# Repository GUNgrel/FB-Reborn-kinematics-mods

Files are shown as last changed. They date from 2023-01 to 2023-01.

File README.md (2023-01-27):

<br/>
<p align="center">
  <a href="https://github.com/GUNgrel/FB-Reborn-kinematics-mods">
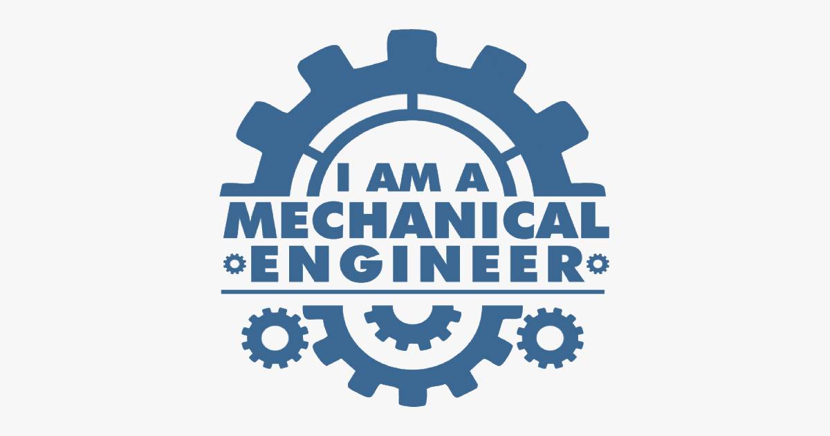
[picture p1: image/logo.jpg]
    
  </a>

  <h3 align="center">Flying Bear Reborn Kinematics mods</h3>

  <p align="center">
    <a href="https://github.com/GUNgrel/FB-Reborn-kinematics-mods"><strong>ВСЕ ФАЙЛЫ ПРОЕКТА</strong></a>
    <br/>
    <br/>
  </p>
</p>

## О проекте

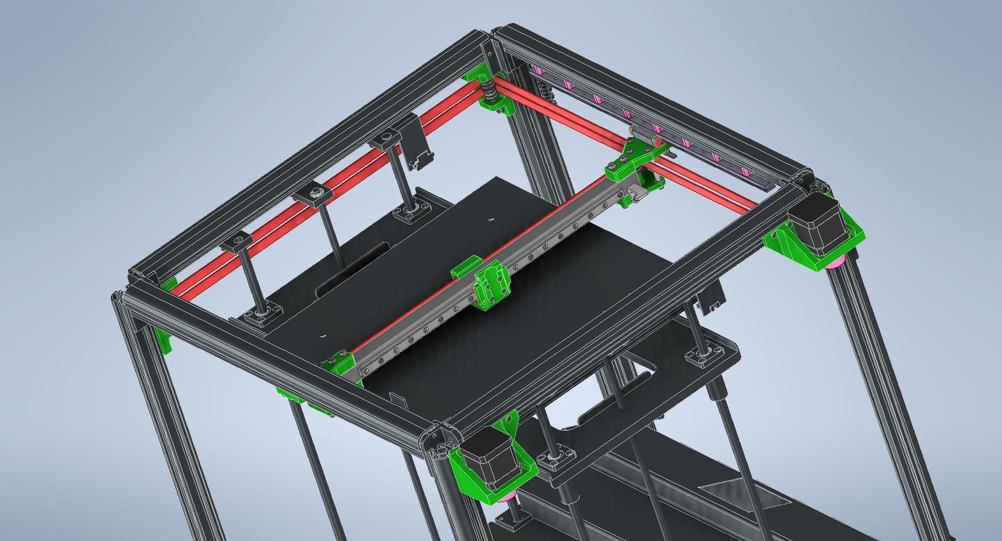
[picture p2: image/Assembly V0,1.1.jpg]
  

  Я очень давно хотел перейти на своём 3д принтере Flying Bear Reborn на рельсы MGN12 и ремни 10 мм, но все существующие проекты так или иначе меня не устраивали.
Поэтому я решил создать собственный проект комплексной замены кинематики по осям Х и У.
  Так сказать "с преферансом и куртизанками" 
  
  Данный проект предусматривает установку головы от [Ruslan P](https://t.me/pavluchenkor) - [Бшня Микшки](https://github.com/pavluchenkor/BearTower)

## Программное обеспечение

I design in Autodesk Inventor 2022

### Что вам понадобится для сборки этого мода:

 ИНСТРУМЕНТЫ
1. Немного прямых рук)
2. Минимальный набор шестигранников.
3. Мини УШМ или ножовка по металлу.
4. Дрель и сверло 3(3.2) и 6 мм.
  
 ПОКУПКИ

   1. [ВЕДОМОСТЬ ПОКУПНЫХ ИЗДЕЛИЙ](https://github.com/GUNgrel/FB-Reborn-kinematics-mods/raw/main/XLS/Purchase_list.xlsx) 

   2. [ВЕДОМОСТЬ КРЕПЁЖНЫХ ИЗДЕЛИЙ](https://github.com/GUNgrel/FB-Reborn-kinematics-mods/raw/main/XLS/Screws_and_nuts.xlsx)

### СБОРКА

Сборка надо начинать с печати всех или нужны вам деталей.

Если у вас уже установлены рельсы снизу профилей, то проставки для рельс MGN12 печатать не надо.

### <b>Балка У</b>

Для определения сторон – принтер ориентирован при просмотре моторами к зрителю.

Для сборки балки У

Вместо карбоновой трубы возможно использовать профиль 2020.
Длинна трубы или профиля 400 мм. За счёт  пропилов возможна небольшая регулировка по длинне балки в сборе. Принтеры немного отличаются друг от друга.

1.	Если вы используете карбоновую квадрат трубу, то в ней необходимо пропилить с торцов паз шириной 6 мм и длиной 25мм. 

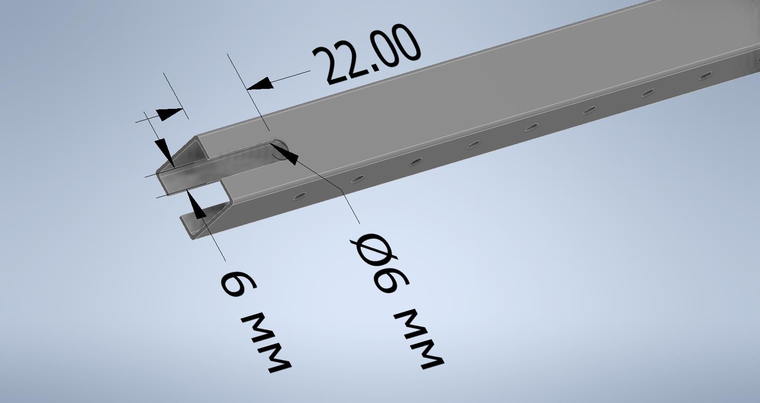
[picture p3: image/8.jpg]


Просверлите отверстия крепления рельсы к балке, используя рельсу для разметки (можно крепить через одно отверстие). 

Для крепления рельсы распечатайте полосу под гайки М3 - nut strip for MGN9 rail. 

Если используете рельсу MGN12 то полоса под гайки - nut strip for MGN12 rail.

Вместо карбоновой трубы возможно использовать профиль 2020.

2.	Далее собираете кронштейны балки. Правый кронштейн имеет отверстия для крепления флажков концевиков Х и У. 

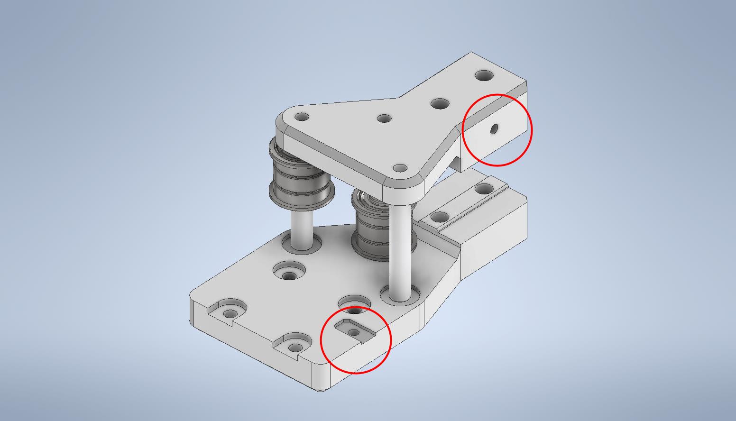
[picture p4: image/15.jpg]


Левый кронштейн без отверстий под флажки концевиков 

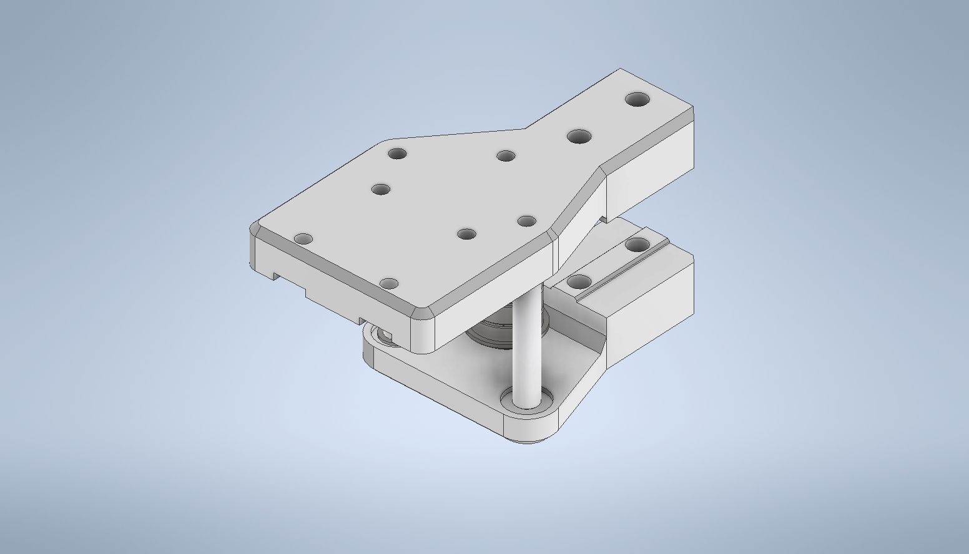
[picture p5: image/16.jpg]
 

Для сборки кронштейнов понадобятся детали:

Штифт 5х30 (резьба М3 с двух сторон) – 6шт

Подшипники F695ZZ -  8 шт

Подшипник 695ZZ – 4 шт.

Винт М3х12 – 12 шт.

Винт М4х50 – 4 шт.

Шайбы М3- 24 шт.

Шайбы М4- 8 шт.

Гайки М4 самоконтрящиеся – 4 шт.

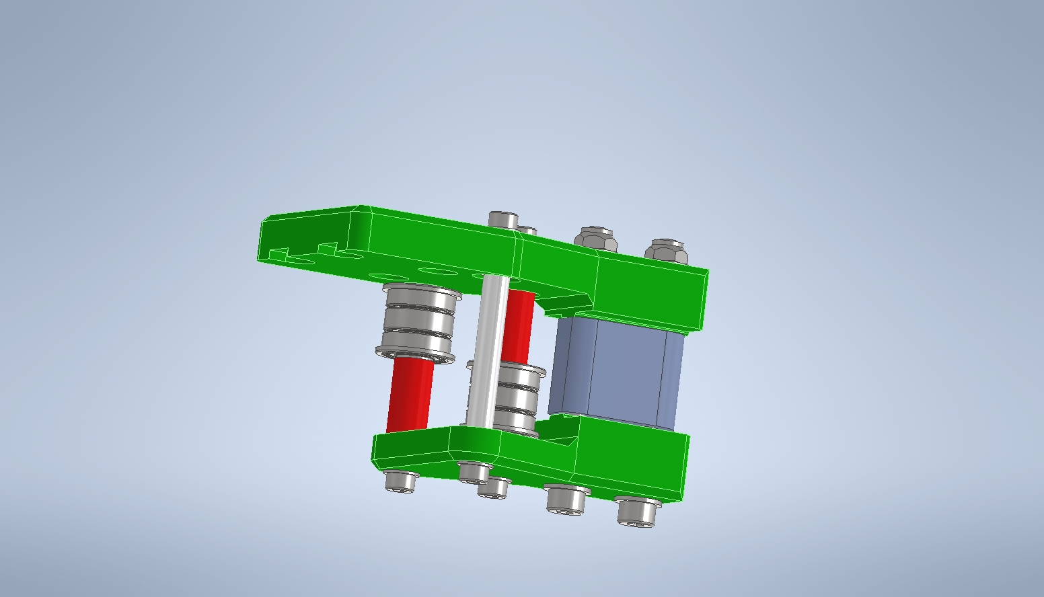
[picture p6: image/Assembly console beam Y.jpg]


Подробнее смотри файл сборки -  [Assembly console beam Y](https://github.com/GUNgrel/FB-Reborn-kinematics-mods/raw/main/STEPs/Assembly_console_beam_Y.stp)

3.	Сборка балки Y

Вставьте балку с рельсой в кронштейны. Винты М4 затягивать после установки на рельсы MGN12 и выставления перпендикулярности. 

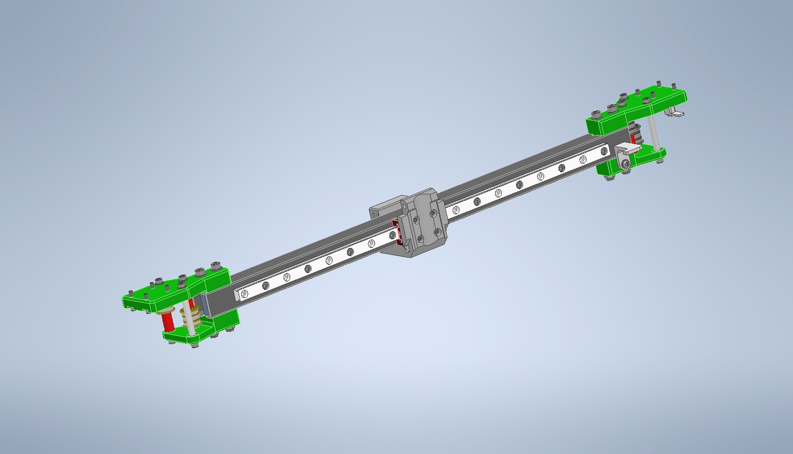
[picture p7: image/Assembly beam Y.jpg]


Подробнее смотри файл сборки - [Assembly beam Y](https://github.com/GUNgrel/FB-Reborn-kinematics-mods/raw/main/STEPs/Assembly_beam_Y.stp)

### Сборка рельс оси Х

Печатаем проставки – 16 шт (из расчёта на рельсу длинной 400мм). Вставляем закладные гайки М3. 

Крепим по 8 шт. с каждой стороны рамы винтами М4х10 и Т-гайками М4.  

НЕ ОБТЯГИВАТЬ.

Крепим рельсу c кареткой на проставки винтами М3х12 

НЕ ОБТЯГИВАТЬ.

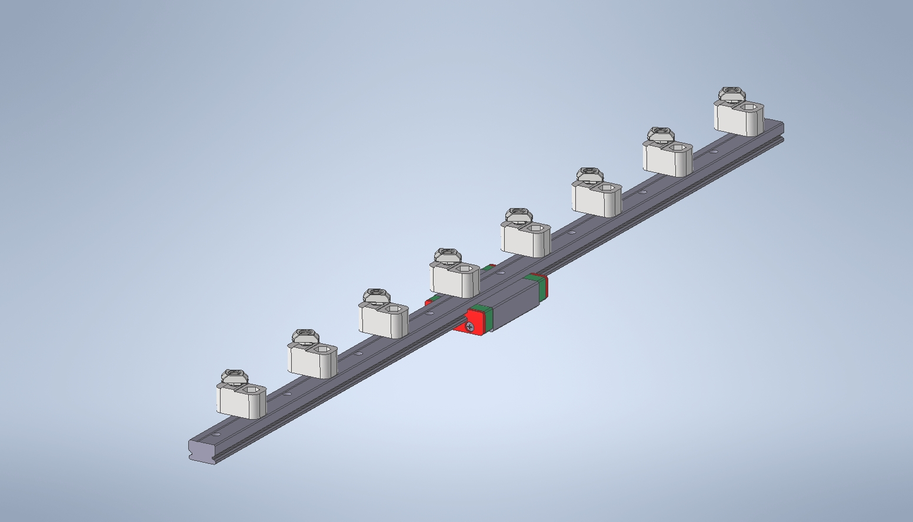
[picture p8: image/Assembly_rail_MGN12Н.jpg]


Подробнее смотри файл сборки - [Assembly_rail_MGN12Н](https://github.com/GUNgrel/FB-Reborn-kinematics-mods/raw/main/STEPs/Assembly_rail_MGN12Н.stp)

### Настройка параллельности и перпендикулярности осей Х и У

Готовьтесь много крутить крепёж…

Сначала выставьте рельсы приблизительно параллельно друг другу, я использовал кусок вала 8 мм. Главное одинаковое расстояние. 

Затем смонтируйте собранную балку У на рельсы Х. Кронштейн балки У сильно не обтягивать. Не затянутый крепёж карбоновой трубы позволит немного смещать её вдоль оси Y, что даст точно выставить расстояние между кронштейнами балки Y.

Теперь с помощью угольника выставите 90 градусов между рельсой Х и рельсой У.

Затяните крепёж кронштейна балки Y с той стороны, где установлен угольник.

Двигайте вперёд и назад балку Y. Она выставит на нужное расстояние вторую рельсу. 

Затяните весь крепёж. Без фанатизма) Детали пластиковые. Лучше добавьте синий фиксатор резьбы.

### МОТОРЫ

Есть два варианта расположения моторов 

## Снаружи 

В этом случае кронштейны разные. Печатать отдельно

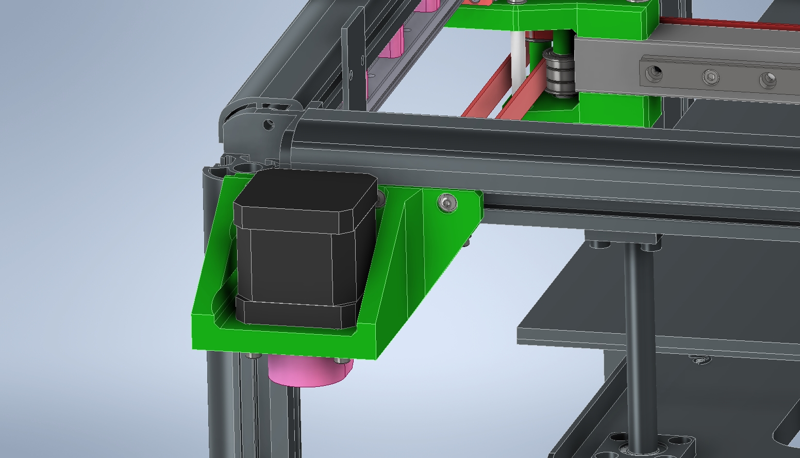
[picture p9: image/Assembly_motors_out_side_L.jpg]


[Console_left_motor](https://github.com/GUNgrel/FB-Reborn-kinematics-mods/blob/main/STEPs/Console_left_motor.stp)

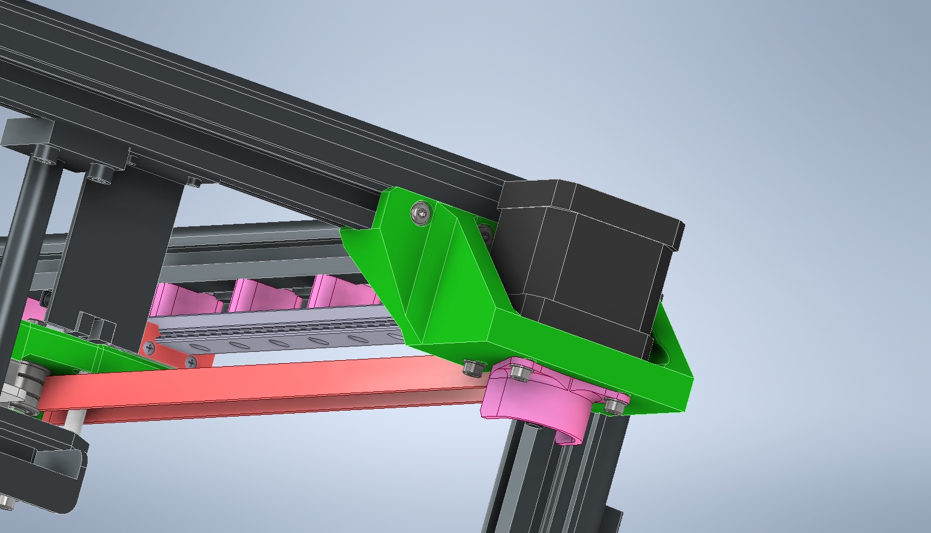
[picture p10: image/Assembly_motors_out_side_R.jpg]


[Console_right_motor](https://github.com/GUNgrel/FB-Reborn-kinematics-mods/blob/main/STEPs/Console_right_motor.stp)

## Внутри 

В этом слусае кронштейны одинаковые с права и лева. Один монтируется ниже другого. Печаталь зеркально на поддержках. 

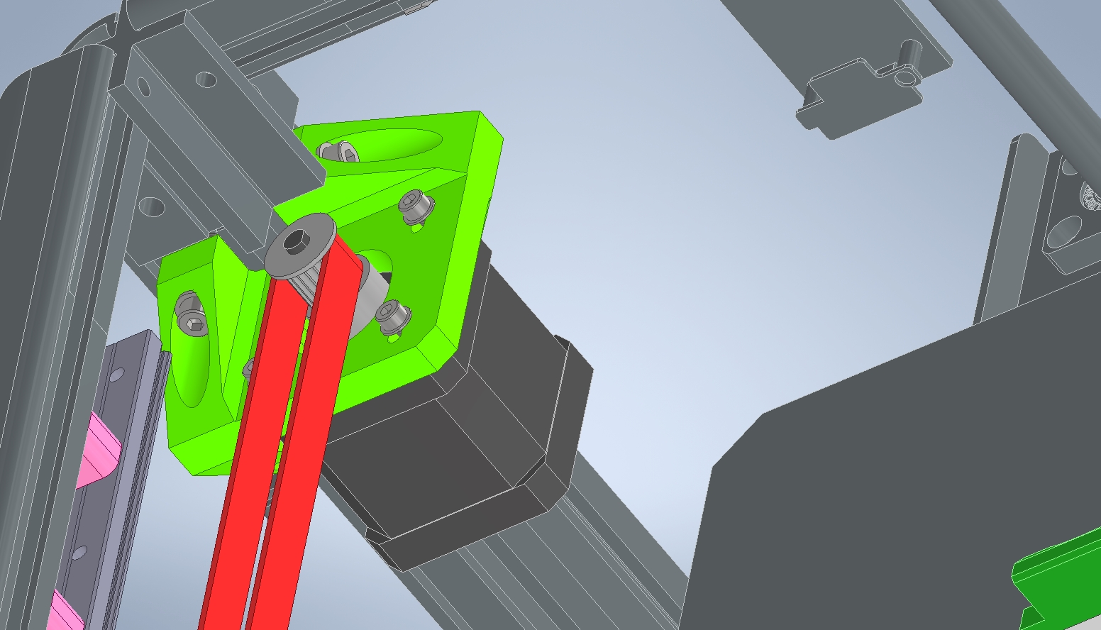
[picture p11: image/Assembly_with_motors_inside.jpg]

 
[Console_moto_inside](https://github.com/GUNgrel/FB-Reborn-kinematics-mods/blob/main/STEPs/Console_moto_inside.stp)

## Автор

* **Alexey Khripyakov** - *Engineer constructor* - [Telegram](https://t.me/gungrel)

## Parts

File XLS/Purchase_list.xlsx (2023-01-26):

Шайбы 5х7 разной толщны | https://aliexpress.ru/item/1005003719920719.html?sku_id=12000026928248768
Шайбы 3х7х0.5 | https://aliexpress.ru/item/1005003719920719.html?sku_id=12000026928248768
Втулка дистанционная М5х9х14 | https://aliexpress.ru/item/32542380485.html?sku_id=12000028149918777 | Можно напечатать
Штифт 5х30 (резьба М3 с двух сторон) | https://aliexpress.ru/item/1005002348335932.html?sku_id=12000020218389252
Карбоновая квадрат труба 20х20 стенка 1 мм | https://aliexpress.ru/item/1005003695712458.html?sku_id=12000026837917258
F695ZZ подшипник | https://aliexpress.ru/item/32804175494.html?sku_id=64190317577
695ZZ подшипник | https://aliexpress.ru/item/558040550.html?sku_id=12000025647486835
Шкив отверстие 5мм под ремень 10мм | https://aliexpress.ru/item/4000454449561.html?sku_id=10000001855896885
Ремень ГРМ POWGE GT2 10ММ 5 МЕТРОВ | https://aliexpress.ru/item/1005004244320781.html?sku_id=12000028506074812
Рельсы MGN | https://aliexpress.ru/item/1005004535281832.html?sku_id=12000029510101691

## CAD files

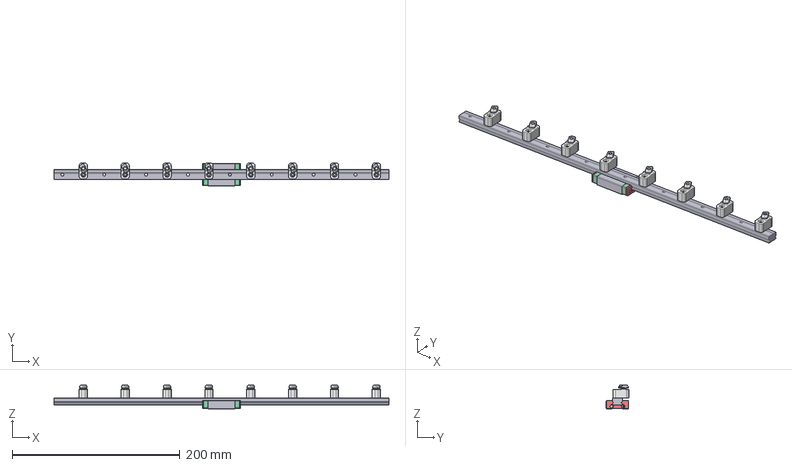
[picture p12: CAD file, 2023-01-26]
STEPs/Assembly_rail_MGN12Н.stp
400.0 x 27.4 x 28.6 mm
PRODUCT_NAME_1_MIR2
PRODUCT_NAME_2_MIR2
PRODUCT_NAME_3_MIR2
PRODUCT_NAME_4_MIR2
PRODUCT_NAME_5_MIR2
PRODUCT_NAME_6_MIR2
PRODUCT_NAME_7_MIR2
PRODUCT_NAME_8_MIR2
PRODUCT_NAME_9_MIR2
PRODUCT_NAME_10_MIR2
Проставка рельсы_ MIR2 x 8
ISO 4762 - M4 x 10 x 8
ISO 4762 - M3 x 12 x 8
ISO 4032 - M3 x 8
M4 T slot nut - 2020 x 8

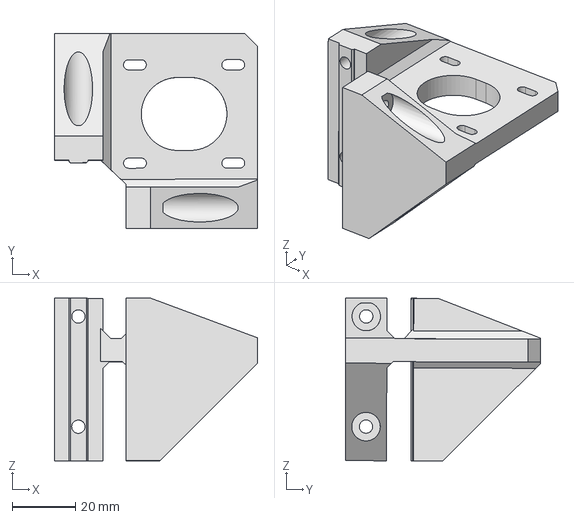
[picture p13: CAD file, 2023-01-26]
STEPs/Console_moto_inside.stp
64.0 x 61.6 x 51.3 mm

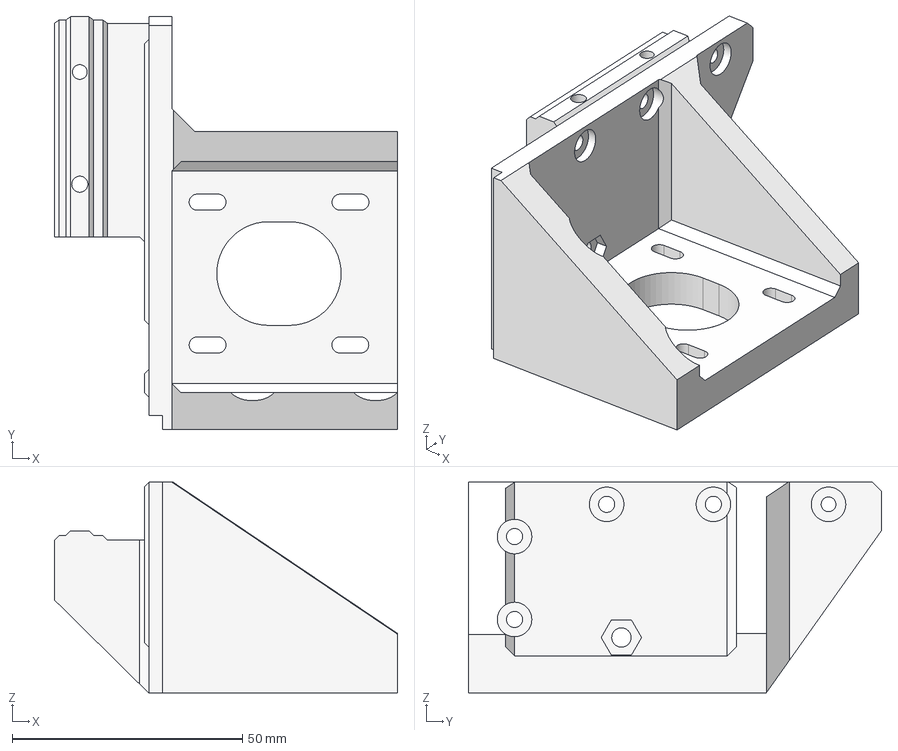
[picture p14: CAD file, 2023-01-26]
STEPs/Console_left_motor.stp
74.5 x 89.7 x 45.7 mm

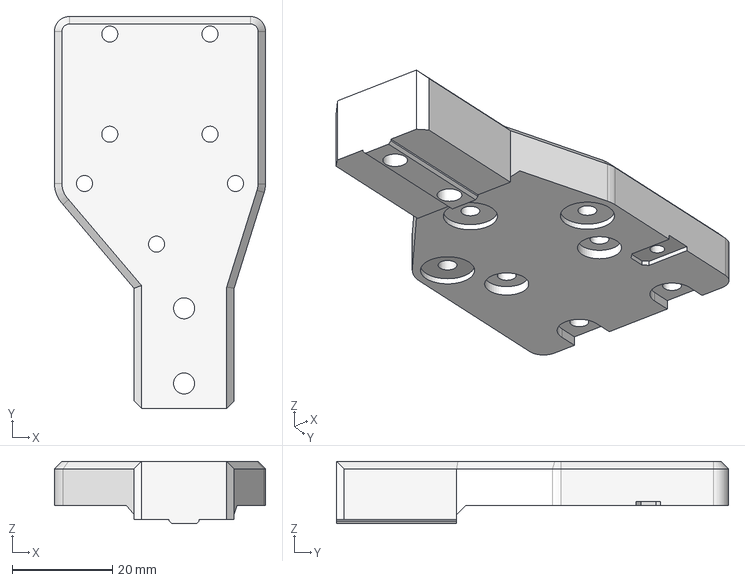
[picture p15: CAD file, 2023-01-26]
STEPs/console_beam_Y_upper_MGN12H-with_flag.stp
42.1 x 78.2 x 12.4 mm

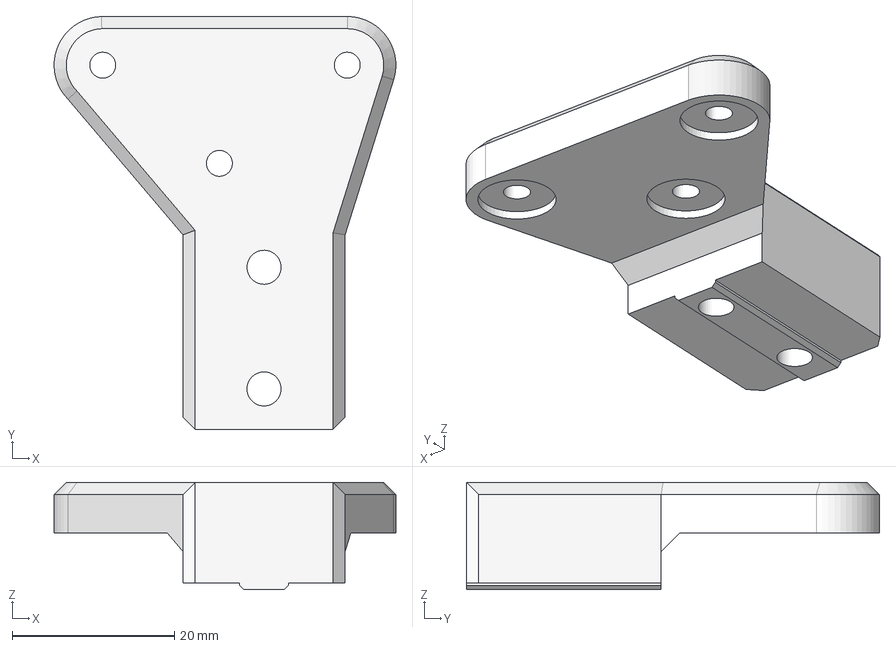
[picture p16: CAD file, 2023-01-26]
STEPs/console_beam_Y_lower_MGN12H.stp
42.1 x 50.9 x 13.2 mm

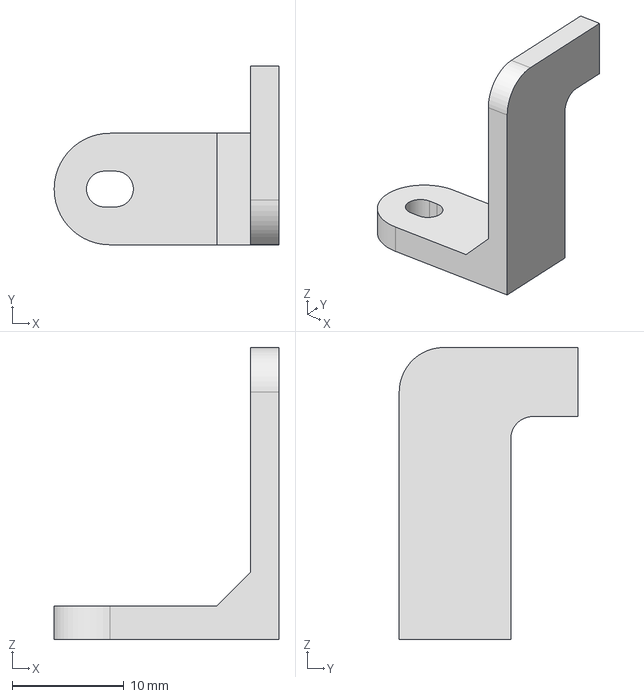
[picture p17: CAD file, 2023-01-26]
STEPs/limit_switch_flag_Y.stp
20.1 x 16.0 x 26.2 mm

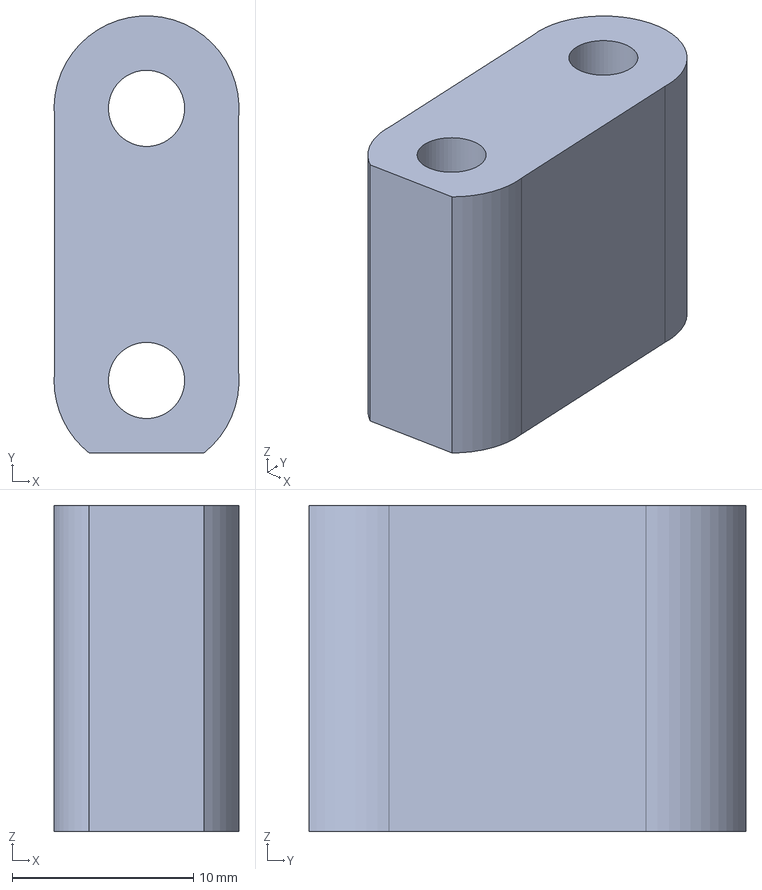
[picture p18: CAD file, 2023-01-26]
STEPs/beam_spacer.stp
10.2 x 24.1 x 18.0 mm

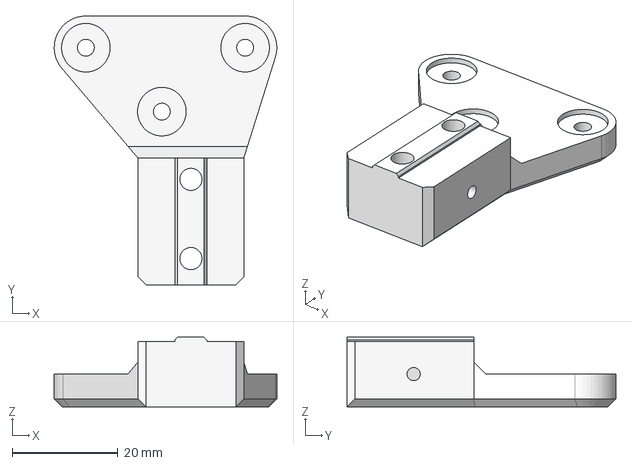
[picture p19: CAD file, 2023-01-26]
STEPs/console_beam_Y_lower_MGN12H_with_flag.stp
42.1 x 50.9 x 13.2 mm

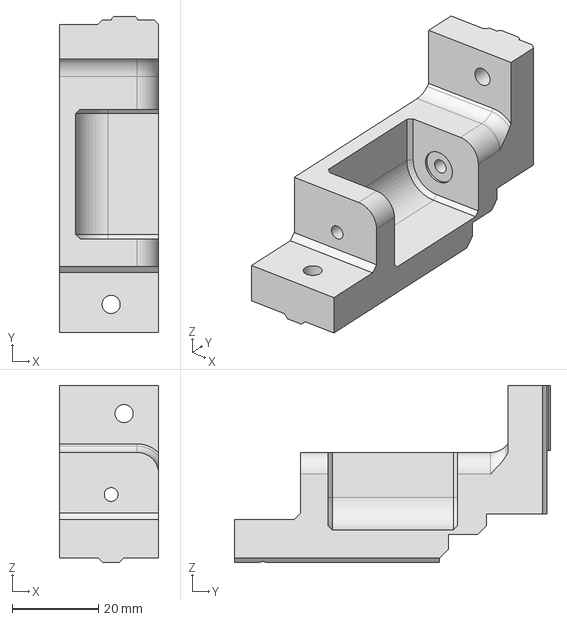
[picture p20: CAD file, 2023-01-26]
STEPs/bypass_roller_mount.stp
23.0 x 73.1 x 41.0 mm

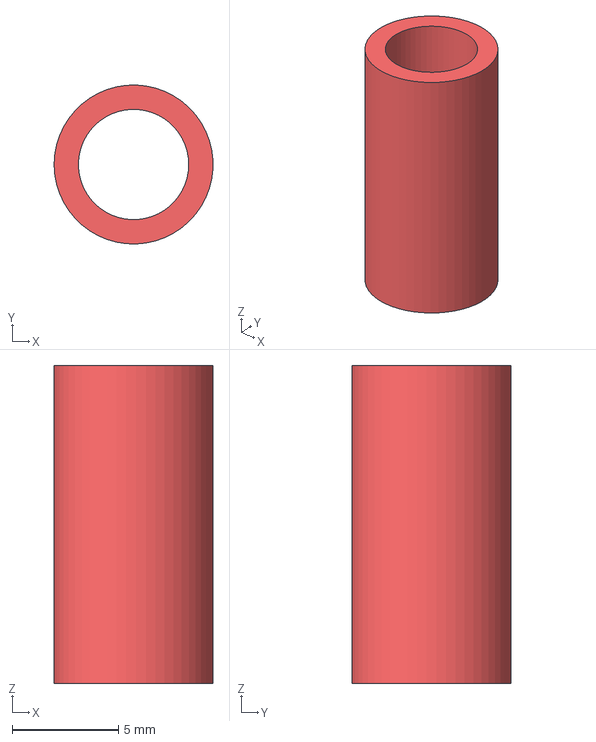
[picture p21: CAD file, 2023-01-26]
STEPs/spacer_sleeve_5х7х14.stp
7.49 x 7.50 x 15.0 mm

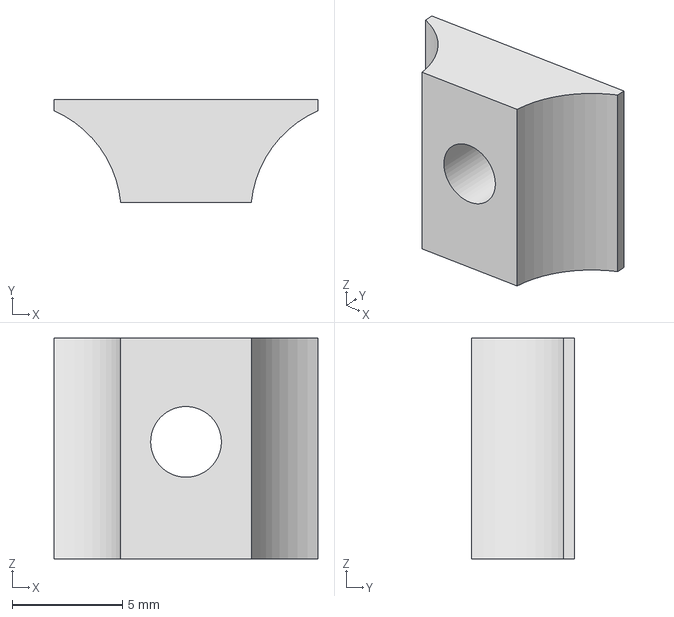
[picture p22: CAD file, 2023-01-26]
STEPs/Belt_retainer_for_carriage.stp
11.9 x 4.64 x 10.0 mm

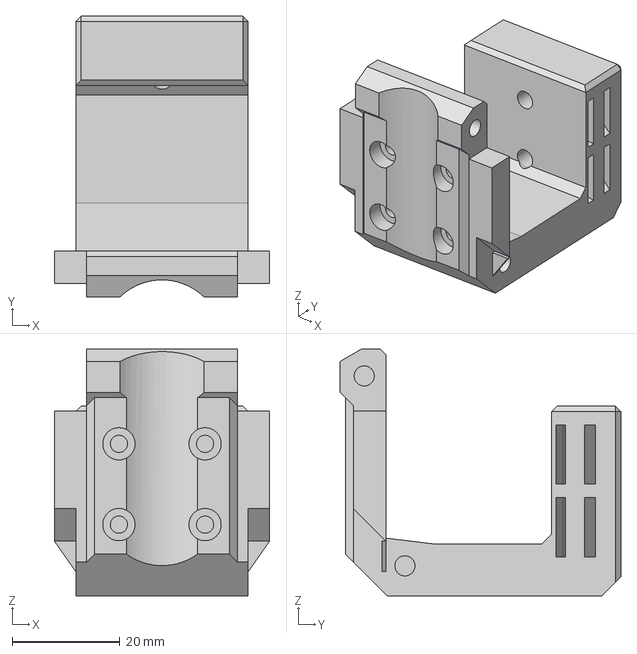
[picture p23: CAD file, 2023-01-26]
STEPs/carriage_for_MGN9H_10mm_belt.stp
40.0 x 52.2 x 45.9 mm

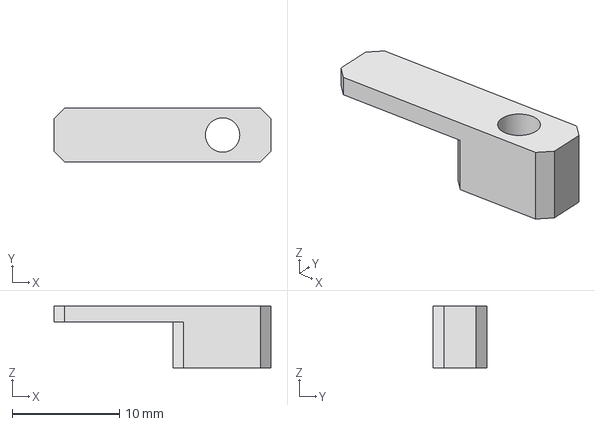
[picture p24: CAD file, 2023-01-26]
STEPs/limit_switch_flag_Х.stp
20.2 x 5.00 x 5.75 mm

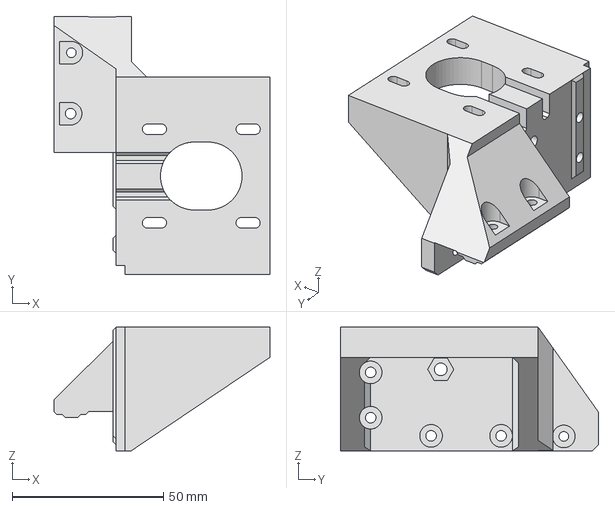
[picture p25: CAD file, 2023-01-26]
STEPs/Console_right_motor.stp
71.5 x 85.4 x 41.0 mm

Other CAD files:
STEPs/console_beam_Y_upper_MGN12H.stp
STEPs/belt_cover.stp
STEPs/nut_strip_for_MGN12_rail.stp
STEPs/nut_strip_for_MGN9_rail.stp

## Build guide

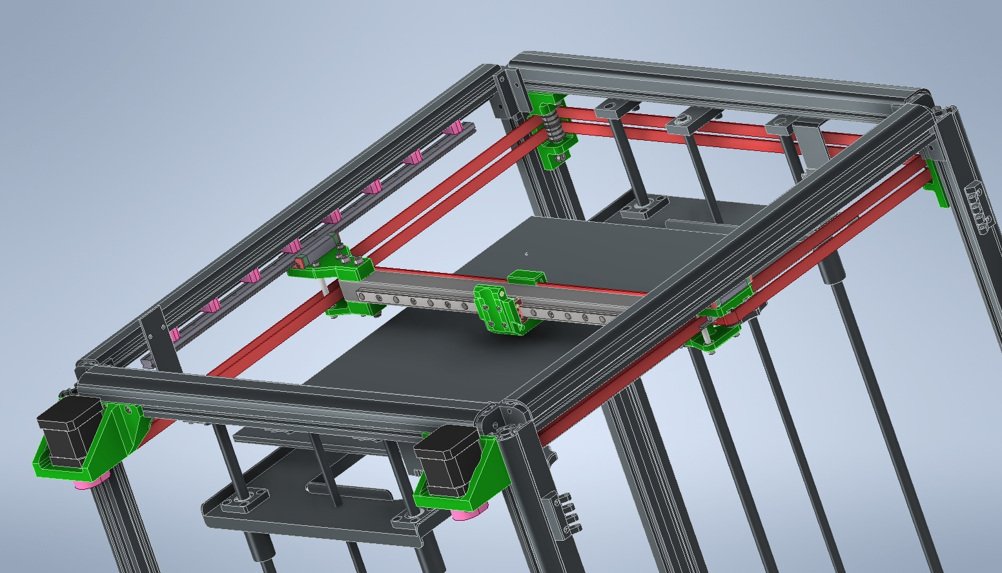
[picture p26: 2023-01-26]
image/Assembly V0,1.jpg

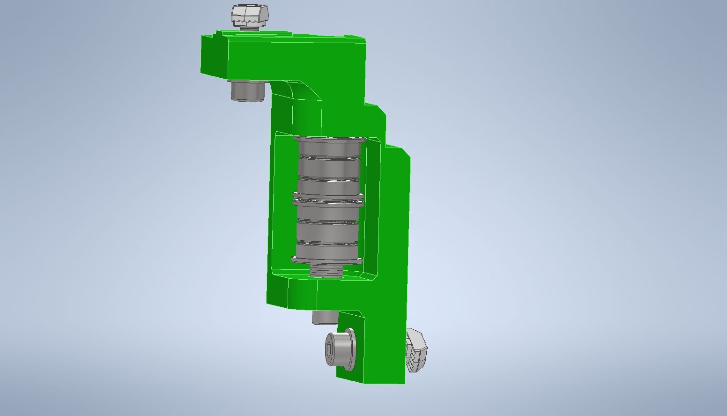
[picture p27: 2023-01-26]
image/Assembly bypass rollert.jpg
